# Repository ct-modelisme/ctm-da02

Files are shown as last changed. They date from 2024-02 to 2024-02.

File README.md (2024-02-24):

# CTM-DA02: Blacksmith environment command

The CTM-DA02 is a blacksmith electronic controller for modelrailway projects.
This electronic card is compatible with DCC & AC/DC train layouts.

## Licenses

The hardware is released under OpenHardware principes, and the software under OpenSource principes.

 - Hardware (PCB): [Creative Commons Attribution-ShareAlike 4.0 International License](http://creativecommons.org/licenses/by-sa/4.0/)
 - Software (Firmware): [GNU General Public License v3](https://www.gnu.org/licenses/)

## Current releases

 - Hardware (PCB): version 1.0
 - Software (Firmware): version 1.0

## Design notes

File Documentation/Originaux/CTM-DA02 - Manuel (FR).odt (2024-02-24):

CTM-DA02

Commande de forge

La carte CTM-DA02 est une carte de commande de forge. Elle permet de commander un forgeron animé (ex : Viessmann® 1514) et une LED imitation flamme (ex : Lapierre-Modélisme 10L5FL) tout en jouant un fichier son.

En cas de bogue, ou simplement si vous avez des suggestions, merci de me contacter à l’adresse :

cyrille.toulet@linux.com

# Fonctionnalités

- Commande par DCC ou par boutons poussoirs (déportés et/ou sur la carte) ;
- Sortie forgeron (12V) et LED imitation flamme (3V) ;
- Lecture d’un fichier audio lors de l’animation ;
- Fonctionnalité d’apprentissage dynamique des adresses DCC ;
- Connexion USB série 115 200 bauds (optionnelle).

# Montage

## Aperçu du montage minimal

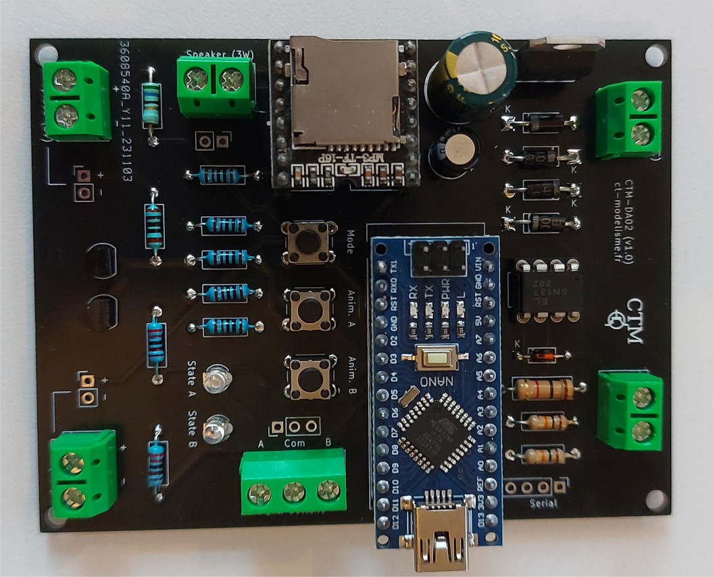
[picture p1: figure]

## Liste des composants

## Ordre de montage recommandé

Comme pour n’importe quel circuit électronique, commencez des composants les moins hauts pour terminer sur les plus hauts : diode 1N4148 (D5), puis résistances 1/4 W (toutes sauf R1), puis diodes 1N4007 (D1 à D4) et résistance 1W (R1). Ensuite, boutons poussoirs (SW1-3), supports de CI (s’il y en a), opto-coupleur (U2), LEDs (D6 et D7) , transistors (Q1 et Q2), connecteurs et borniers à vis, condensateurs 6.3mm (C2), condensateurs 10mm (C1) et enfin, le régulateur de tension 5V (U1). Terminez par enficher l’arduino (A1) et le lecteur audio (U3).

## Options

En fonction du câblage de votre réseau, vous pouvez opter pour presque chaque entrée/sortie entre tiliser un bornier, utiliser un connecteur tulippe ou à broche, ou encore souder des fils directement à la place du connecteur.

Ainsi, les connecteurs J3 et J4 sont reliés, ainsi que J6 avec J7, J8 avec J9, et J10 avec J11.

Pour rendre démontable le lecteur audio ou l’arduino, vous pouvez également ajouter les supports femelles préconisés dans la liste des compostants.

# Installation

## Firmware

Compilez et envoyez le firmware de la carte vers un arduino nano à partir de du logiciel Arduino SDK. Puis enfichez l’arduino sur le connecteur A1.

## Fixation

La carte électronique dispose de 4 trous de montage M3 pour être fixée avec des vis (avec ou sans entretoises) ou des supports édhésifs.

## Connexions

Connectez une alimentation de 12V DC sur le connecteur « Power » (peu importe la polarité). Connectez le bus JK sur le connecteur « DCC » (pas de polarité particulière). Connectez le haut-parleur (2 à 3W min sous 4 ou 8 Ohm) sur le connecteur « Spealer », la LED simulation de flame sur le connecteur « Fireplace » et le personnage animé sur le connecteur « Envil ». Vous pouvez aussis déporter un poutton poussoir pour lancer l’animation. Dans ce cas, connectez le sur le connecteur « Ext. buttons ».

# Utilisation

## Apprentissage d’adresse DCC

Pour entrer en mode apprentissage d’adresse, appuyez 3 secondes sur le bouton « Mode ». La LED « L » de l’arduino s’allume.

Envoyez une commande d’accessoire sur l’adresse voulue depuis votre centrale DCC. Cette adresse sera mémorisée par la carte comme adresse DCC de la carte.

Une fois l’adresse apprise, la carte repasse en mode normal et la LED « L » de l’arduino s’éteint.

Astuce : vous pouvez quitter à tout moment le mode apprentissage en appuyant 2 secondes sur le bouton « Mode ».

## Moniteur série & réinitialisation de la carte

Lorsque vous branchez un câble USB à l’arduino, et que vous lancez le moniteur série à 115 200 bauds, un appuis court sur le bouton « Mode » imprimera la configuration courante de la carte.

Différentes informations seront affichée suite à plusieurs appuis sur le bouton « Mode », jusqu’à revenir en fonctionnement normal.

Astuce : lors que vous utilisez le moniteur série, il est possible de réinitialiser la carte en tapant la commande « reset » dans la console. Cette commande aura pour effet de réinitialiser la carte à ses paramètres d’usine.

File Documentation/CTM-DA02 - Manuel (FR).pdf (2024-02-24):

# CTM-DA02

## Commande de forge

La carte CTM-DA02 est une carte de commande de forge. Elle permet de commander un forgeron animé (ex : Viessmann® 1514) et une LED imitation flamme (ex : Lapierre-Modélisme 10L5FL) tout en jouant un fichier son.
En cas de bogue, ou simplement si vous avez des suggestions, merci de me contacter à l’adresse : cyrille.toulet@linux.com

## Fonctionnalités

- Commande par DCC ou par boutons poussoirs (déportés et/ou sur la carte) ;
- Sortie forgeron (12V) et LED imitation flamme (3V) ;
- Lecture d’un fichier audio lors de l’animation ;
- Fonctionnalité d’apprentissage dynamique des adresses DCC ;
- Connexion USB série 115 200 bauds (optionnelle).

## Montage

## Aperçu du montage minimal

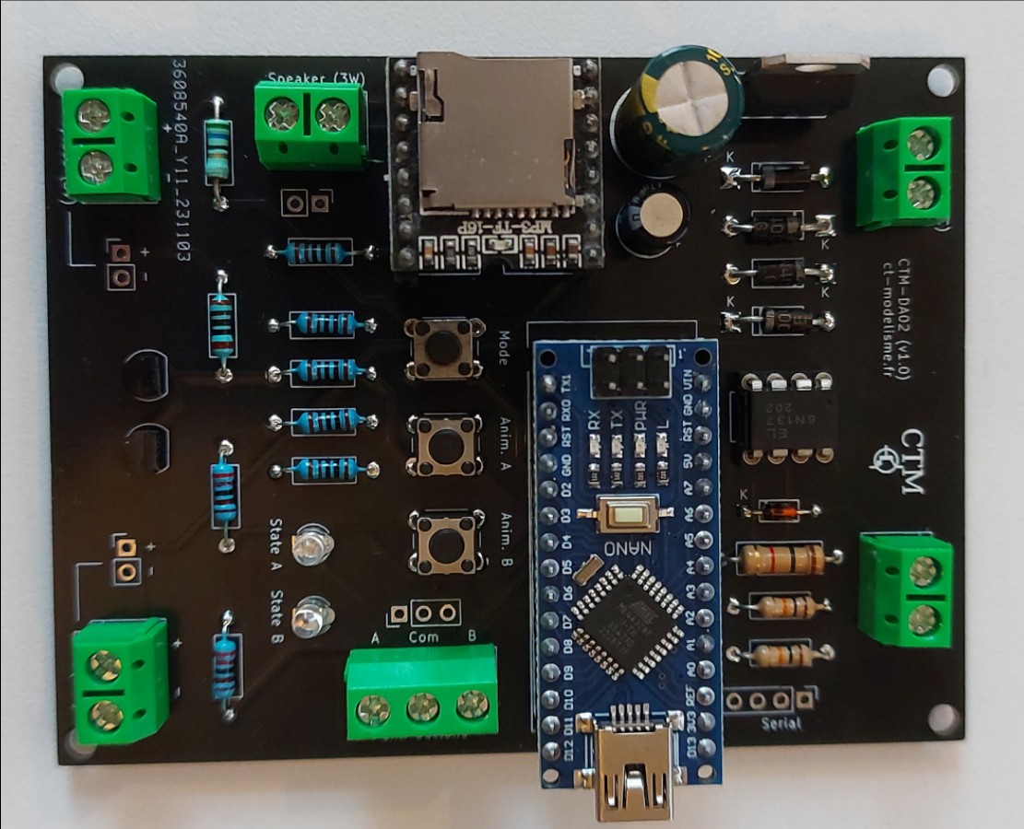
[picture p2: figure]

## Liste des composants

Options | Qté | Composant
A1 | 2 | Connecteur 15 pins femelle (pour rendre l’arduino démontable)
U3 | 2 | Connecteur 8 pins femelle (pour rendre le DFPlayer démontable)
J3 et/ou J4 | - | Soit rien, soit l'un, soit l'autre, soit les deux
J5 | - | Pour connexion série
J6 et/ou J7 | - | Soit rien, soit l'un, soit l'autre, soit les deux
J8 et/ou J9 | - | Soit rien, soit l'un, soit l'autre, soit les deux
J10 et/ou J11 | - | Soit rien, soit l'un, soit l'autre, soit les deux
Références | Composant | Quantité | Description
A1 | Arduino Nano | 1 | Support optionnel
C1 | 470µF | 1 | Diamètre 10mm, pas de 5mm
C2 | 10µF | 1 | Diamètre 6.3mm, pas de 2.5mm
D1, D2, D3, D4 | 1N4007 | 4
D5 | 1N4148 | 1
D6, D7 | LED | 2 | Diamètre 3mm
J1, J2, J7, J9, J10 | Bornier à vis 1x2 | 5 | Pas de 5.08mm
J3 | Bornier à vis 1x3 | 1 | Pas de 5.08mm
J4 | Connecteur tulipe 1x3 | 1 | Optionnel
J5 | Connecteur tulipe 1x4 | 1 | Optionnel
J6, J8, J11 | Connecteur tulipe 1x2 | 3 | Optionnel
Q1, Q2 | BC547 | 2 | Boîtier TO-92 en ligne
R1 | 1k (1W) | 1
R2, R3 | 10k | 2
R4, R5, R6, R7, R12 | 1k | 5
R8 | 56 | 1
R9 | 100 | 1
R10, R11 | 2.2k | 2
SW1, SW2, SW3 | Embeded push btn | 3 | Bouton 6mm
U1 | LM7805 (1A) | 1 | Boîtier TO-220
U2 | 6N137 | 1 | DIP-8
U3 | DFPlayerMini | 1 | Ou autre MP3-TF-16P
- | Carte micro-SD | 1 | Une petite suffira (ex : 512 Mo)
- | Haut parleur 2 à 3 W | 1 | 4 ou 8 Ohm
- | PCB CTM-DA02 | 1 | Carte électronique CTM-DA02

## Ordre de montage recommandé

Comme pour n’importe quel circuit électronique, commencez des composants les moins hauts pour terminer sur les plus hauts : diode 1N4148 (D5), puis résistances 1/4 W (toutes sauf R1), puis diodes 1N4007 (D1 à D4) et résistance 1W (R1). Ensuite, boutons poussoirs (SW1-3), supports de CI (s’il y en a), opto-coupleur (U2), LEDs (D6 et D7) , transistors (Q1 et Q2), connecteurs et borniers à vis, condensateurs 6.3mm (C2), condensateurs 10mm (C1) et enfin, le régulateur de tension 5V (U1). Terminez par enficher l’arduino (A1) et le lecteur audio (U3).

## Options

En fonction du câblage de votre réseau, vous pouvez opter pour presque chaque entrée/sortie entre tiliser un bornier, utiliser un connecteur tulippe ou à broche, ou encore souder des fils directement à la place du connecteur.
Ainsi, les connecteurs J3 et J4 sont reliés, ainsi que J6 avec J7, J8 avec J9, et J10 avec J11.
Pour rendre démontable le lecteur audio ou l’arduino, vous pouvez également ajouter les supports femelles préconisés dans la liste des compostants.

## Installation

## Firmware

Compilez et envoyez le firmware de la carte vers un arduino nano à partir de du logiciel Arduino SDK. Puis enfichez l’arduino sur le connecteur A1.

## Fixation

La carte électronique dispose de 4 trous de montage M3 pour être fixée avec des vis (avec ou sans entretoises) ou des supports édhésifs.

## Connexions

Connectez une alimentation de 12V DC sur le connecteur « Power » (peu importe la polarité). Connectez le bus JK sur le connecteur « DCC » (pas de polarité particulière). Connectez le haut-parleur (2 à 3W min sous 4 ou 8 Ohm) sur le connecteur « Spealer », la LED simulation de flame sur le connecteur « Fireplace » et le personnage animé sur le connecteur « Envil ». Vous pouvez aussis déporter un poutton poussoir pour lancer l’animation. Dans ce cas, connectez le sur le connecteur « Ext. buttons ».

## Utilisation

## Apprentissage d’adresse DCC

Pour entrer en mode apprentissage d’adresse, appuyez 3 secondes sur le bouton « Mode ». La LED « L » de l’arduino s’allume.
Envoyez une commande d’accessoire sur l’adresse voulue depuis votre centrale DCC. Cette adresse sera mémorisée par la carte comme adresse DCC de la carte.
Une fois l’adresse apprise, la carte repasse en mode normal et la LED « L » de l’arduino s’éteint. Astuce : vous pouvez quitter à tout moment le mode apprentissage en appuyant 2 secondes sur le bouton « Mode ».

## Moniteur série & réinitialisation de la carte

Lorsque vous branchez un câble USB à l’arduino, et que vous lancez le moniteur série à 115 200 bauds, un appuis court sur le bouton « Mode » imprimera la configuration courante de la carte. Différentes informations seront affichée suite à plusieurs appuis sur le bouton « Mode », jusqu’à revenir en fonctionnement normal.
Astuce : lors que vous utilisez le moniteur série, il est possible de réinitialiser la carte en tapant la commande « reset » dans la console. Cette commande aura pour effet de réinitialiser la carte à ses paramètres d’usine.

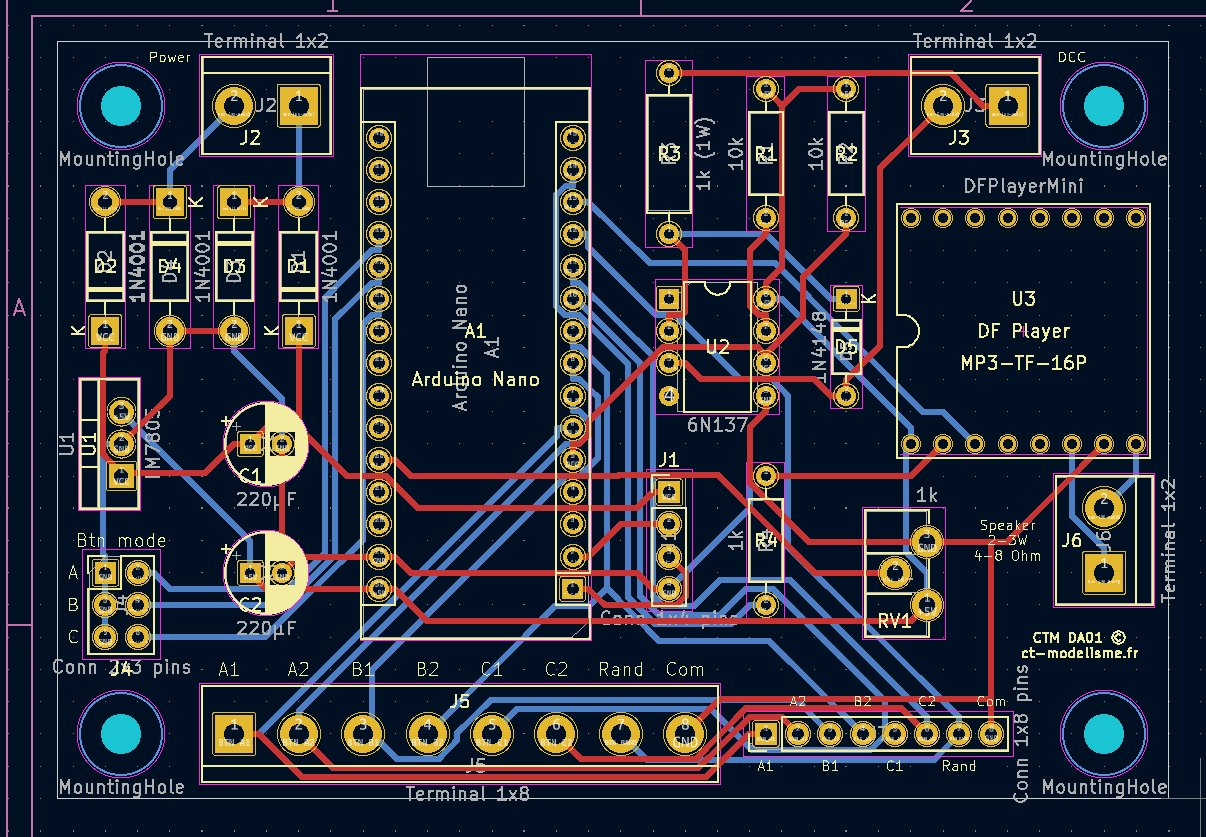
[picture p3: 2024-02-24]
Arduino/CTM-DA02/PCB DA01.PNG

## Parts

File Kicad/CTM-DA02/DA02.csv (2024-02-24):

Source: | C:\Users\Cyrille\Documents\KiCad\CTM - DA02\DA02\DA02.kicad_sch
Date: | 28/10/2023 11:12:37
Tool: | Eeschema (6.0.6)
Generator: | C:\Program Files\KiCad\6.0\bin\scripting\plugins/bom_csv_grouped_by_value.py
Component Count: | 45
Individual Components:
Item | Qty | Reference(s) | Value | LibPart | Footprint | Datasheet
 |  | A1 | Arduino Nano | MCU_Module:Arduino_Nano_v2.x | Module:Arduino_Nano | https://www.arduino.cc/en/uploads/Main/ArduinoNanoManual23.pdf
 |  | C1 | 470µF | Device:C_Polarized | Capacitor_THT:CP_Radial_D10.0mm_P5.00mm | ~
 |  | C2 | 10µF | Device:C_Polarized | Capacitor_THT:CP_Radial_D6.3mm_P2.50mm | ~
 |  | D1 | 1N4001 | Diode:1N4001 | Diode_THT:D_DO-41_SOD81_P10.16mm_Horizontal | http://www.vishay.com/docs/88503/1n4001.pdf
 |  | D2 | 1N4001 | Diode:1N4001 | Diode_THT:D_DO-41_SOD81_P10.16mm_Horizontal | http://www.vishay.com/docs/88503/1n4001.pdf
 |  | D3 | 1N4001 | Diode:1N4001 | Diode_THT:D_DO-41_SOD81_P10.16mm_Horizontal | http://www.vishay.com/docs/88503/1n4001.pdf
 |  | D4 | 1N4001 | Diode:1N4001 | Diode_THT:D_DO-41_SOD81_P10.16mm_Horizontal | http://www.vishay.com/docs/88503/1n4001.pdf
 |  | D5 | 1N4148 | Diode:1N4148 | Diode_THT:D_DO-35_SOD27_P7.62mm_Horizontal | https://assets.nexperia.com/documents/data-sheet/1N4148_1N4448.pdf
 |  | D6 | LED | Device:LED | LED_THT:LED_D3.0mm | ~
 |  | D7 | LED | Device:LED | LED_THT:LED_D3.0mm | ~
 |  | H1 | MountingHole | Mechanical:MountingHole | MountingHole:MountingHole_3.2mm_M3 | ~
 |  | H2 | MountingHole | Mechanical:MountingHole | MountingHole:MountingHole_3.2mm_M3 | ~
 |  | H3 | MountingHole | Mechanical:MountingHole | MountingHole:MountingHole_3.2mm_M3 | ~
 |  | H4 | MountingHole | Mechanical:MountingHole | MountingHole:MountingHole_3.2mm_M3 | ~
 |  | J1 | Terminal 01x02 | Connector:Screw_Terminal_01x02 | TerminalBlock:TerminalBlock_bornier-2_P5.08mm | ~
 |  | J2 | Terminal 01x02 | Connector:Screw_Terminal_01x02 | TerminalBlock:TerminalBlock_bornier-2_P5.08mm | ~
 |  | J3 | Terminal 01x03 | Connector:Screw_Terminal_01x03 | TerminalBlock:TerminalBlock_bornier-3_P5.08mm | ~
 |  | J4 | Connector 01x03 | Connector_Generic:Conn_01x03 | Connector_PinHeader_2.54mm:PinHeader_1x03_P2.54mm_Vertical | ~
 |  | J5 | Connector 01x04 | Connector_Generic:Conn_01x04 | Connector_PinHeader_2.54mm:PinHeader_1x04_P2.54mm_Vertical | ~
 |  | J6 | Connector 01x02 | Connector_Generic:Conn_01x02 | Connector_PinHeader_2.54mm:PinHeader_1x02_P2.54mm_Vertical | ~
 |  | J7 | Terminal 01x02 | Connector:Screw_Terminal_01x02 | TerminalBlock:TerminalBlock_bornier-2_P5.08mm | ~
 |  | J8 | Connector 01x02 | Connector_Generic:Conn_01x02 | Connector_PinHeader_2.54mm:PinHeader_1x02_P2.54mm_Vertical | ~
 |  | J9 | Terminal 01x02 | Connector:Screw_Terminal_01x02 | TerminalBlock:TerminalBlock_bornier-2_P5.08mm | ~
 |  | J10 | Terminal 01x02 | Connector:Screw_Terminal_01x02 | TerminalBlock:TerminalBlock_bornier-2_P5.08mm | ~
 |  | J11 | Connector 01x02 | Connector_Generic:Conn_01x02 | Connector_PinHeader_2.54mm:PinHeader_1x02_P2.54mm_Vertical | ~
 |  | Q1 | BC547 | Transistor_BJT:BC547 | Package_TO_SOT_THT:TO-92_Inline | https://www.onsemi.com/pub/Collateral/BC550-D.pdf
 |  | Q2 | BC547 | Transistor_BJT:BC547 | Package_TO_SOT_THT:TO-92_Inline | https://www.onsemi.com/pub/Collateral/BC550-D.pdf
 |  | R1 | 1k (1W) | Device:R | Resistor_THT:R_Axial_DIN0309_L9.0mm_D3.2mm_P12.70mm_Horizontal | ~
 |  | R2 | 10k | Device:R | Resistor_THT:R_Axial_DIN0207_L6.3mm_D2.5mm_P10.16mm_Horizontal | ~
 |  | R3 | 10k | Device:R | Resistor_THT:R_Axial_DIN0207_L6.3mm_D2.5mm_P10.16mm_Horizontal | ~
 |  | R4 | 1k | Device:R | Resistor_THT:R_Axial_DIN0207_L6.3mm_D2.5mm_P10.16mm_Horizontal | ~
 |  | R5 | 1k | Device:R | Resistor_THT:R_Axial_DIN0207_L6.3mm_D2.5mm_P10.16mm_Horizontal | ~
 |  | R6 | 1k | Device:R | Resistor_THT:R_Axial_DIN0207_L6.3mm_D2.5mm_P10.16mm_Horizontal | ~
 |  | R7 | 1k | Device:R | Resistor_THT:R_Axial_DIN0207_L6.3mm_D2.5mm_P10.16mm_Horizontal | ~
 |  | R8 | 56 | Device:R | Resistor_THT:R_Axial_DIN0207_L6.3mm_D2.5mm_P10.16mm_Horizontal | ~
 |  | R9 | 100 | Device:R | Resistor_THT:R_Axial_DIN0207_L6.3mm_D2.5mm_P10.16mm_Horizontal | ~
 |  | R10 | 2.2k | Device:R | Resistor_THT:R_Axial_DIN0207_L6.3mm_D2.5mm_P10.16mm_Horizontal | ~
 |  | R11 | 2.2k | Device:R | Resistor_THT:R_Axial_DIN0207_L6.3mm_D2.5mm_P10.16mm_Horizontal | ~
 |  | R12 | 1k | Device:R | Resistor_THT:R_Axial_DIN0207_L6.3mm_D2.5mm_P10.16mm_Horizontal | ~
 |  | SW1 | Embeded push btn | Switch:SW_Push | Button_Switch_THT:SW_PUSH_6mm | ~
 |  | SW2 | Embeded push btn | Switch:SW_Push | Button_Switch_THT:SW_PUSH_6mm | ~
 |  | SW3 | Embeded push btn | Switch:SW_Push | Button_Switch_THT:SW_PUSH_6mm | ~
 |  | U1 | LM7805 | Regulator_Linear:LM7805_TO220 | Package_TO_SOT_THT:TO-220-3_Vertical | https://www.onsemi.cn/PowerSolutions/document/MC7800-D.PDF
 |  | U2 | 6N137 | Isolator:6N137 | Package_DIP:DIP-8_W7.62mm | https://docs.broadcom.com/docs/AV02-0940EN
 |  | U3 | DFPlayerMini | CTM:DFPlayerMini | Module:DFRobot_DFPlayerMini_DFR0299 | https://wiki.dfrobot.com/DFPlayer_Mini_SKU_DFR0299
Collated Components:
Item | Qty | Reference(s) | Value | LibPart | Footprint | Datasheet
1 | 1 | A1 | Arduino Nano | MCU_Module:Arduino_Nano_v2.x | Module:Arduino_Nano | https://www.arduino.cc/en/uploads/Main/ArduinoNanoManual23.pdf
2 | 1 | C1 | 470µF | Device:C_Polarized | Capacitor_THT:CP_Radial_D10.0mm_P5.00mm | ~
3 | 1 | C2 | 10µF | Device:C_Polarized | Capacitor_THT:CP_Radial_D6.3mm_P2.50mm | ~
4 | 4 | D1, D2, D3, D4 | 1N4001 | Diode:1N4001 | Diode_THT:D_DO-41_SOD81_P10.16mm_Horizontal | http://www.vishay.com/docs/88503/1n4001.pdf
5 | 1 | D5 | 1N4148 | Diode:1N4148 | Diode_THT:D_DO-35_SOD27_P7.62mm_Horizontal | https://assets.nexperia.com/documents/data-sheet/1N4148_1N4448.pdf
6 | 2 | D6, D7 | LED | Device:LED | LED_THT:LED_D3.0mm | ~
7 | 4 | H1, H2, H3, H4 | MountingHole | Mechanical:MountingHole | MountingHole:MountingHole_3.2mm_M3 | ~
8 | 5 | J1, J2, J7, J9, J10 | Terminal 01x02 | Connector:Screw_Terminal_01x02 | TerminalBlock:TerminalBlock_bornier-2_P5.08mm | ~
9 | 1 | J3 | Terminal 01x03 | Connector:Screw_Terminal_01x03 | TerminalBlock:TerminalBlock_bornier-3_P5.08mm | ~
10 | 1 | J4 | Connector 01x03 | Connector_Generic:Conn_01x03 | Connector_PinHeader_2.54mm:PinHeader_1x03_P2.54mm_Vertical | ~
11 | 1 | J5 | Connector 01x04 | Connector_Generic:Conn_01x04 | Connector_PinHeader_2.54mm:PinHeader_1x04_P2.54mm_Vertical | ~
12 | 3 | J6, J8, J11 | Connector 01x02 | Connector_Generic:Conn_01x02 | Connector_PinHeader_2.54mm:PinHeader_1x02_P2.54mm_Vertical | ~
13 | 2 | Q1, Q2 | BC547 | Transistor_BJT:BC547 | Package_TO_SOT_THT:TO-92_Inline | https://www.onsemi.com/pub/Collateral/BC550-D.pdf
14 | 1 | R1 | 1k (1W) | Device:R | Resistor_THT:R_Axial_DIN0309_L9.0mm_D3.2mm_P12.70mm_Horizontal | ~
15 | 2 | R2, R3 | 10k | Device:R | Resistor_THT:R_Axial_DIN0207_L6.3mm_D2.5mm_P10.16mm_Horizontal | ~
16 | 5 | R4, R5, R6, R7, R12 | 1k | Device:R | Resistor_THT:R_Axial_DIN0207_L6.3mm_D2.5mm_P10.16mm_Horizontal | ~
17 | 1 | R8 | 56 | Device:R | Resistor_THT:R_Axial_DIN0207_L6.3mm_D2.5mm_P10.16mm_Horizontal | ~
18 | 1 | R9 | 100 | Device:R | Resistor_THT:R_Axial_DIN0207_L6.3mm_D2.5mm_P10.16mm_Horizontal | ~
19 | 2 | R10, R11 | 2.2k | Device:R | Resistor_THT:R_Axial_DIN0207_L6.3mm_D2.5mm_P10.16mm_Horizontal | ~
20 | 3 | SW1, SW2, SW3 | Embeded push btn | Switch:SW_Push | Button_Switch_THT:SW_PUSH_6mm | ~
21 | 1 | U1 | LM7805 | Regulator_Linear:LM7805_TO220 | Package_TO_SOT_THT:TO-220-3_Vertical | https://www.onsemi.cn/PowerSolutions/document/MC7800-D.PDF
22 | 1 | U2 | 6N137 | Isolator:6N137 | Package_DIP:DIP-8_W7.62mm | https://docs.broadcom.com/docs/AV02-0940EN
23 | 1 | U3 | DFPlayerMini | CTM:DFPlayerMini | Module:DFRobot_DFPlayerMini_DFR0299 | https://wiki.dfrobot.com/DFPlayer_Mini_SKU_DFR0299

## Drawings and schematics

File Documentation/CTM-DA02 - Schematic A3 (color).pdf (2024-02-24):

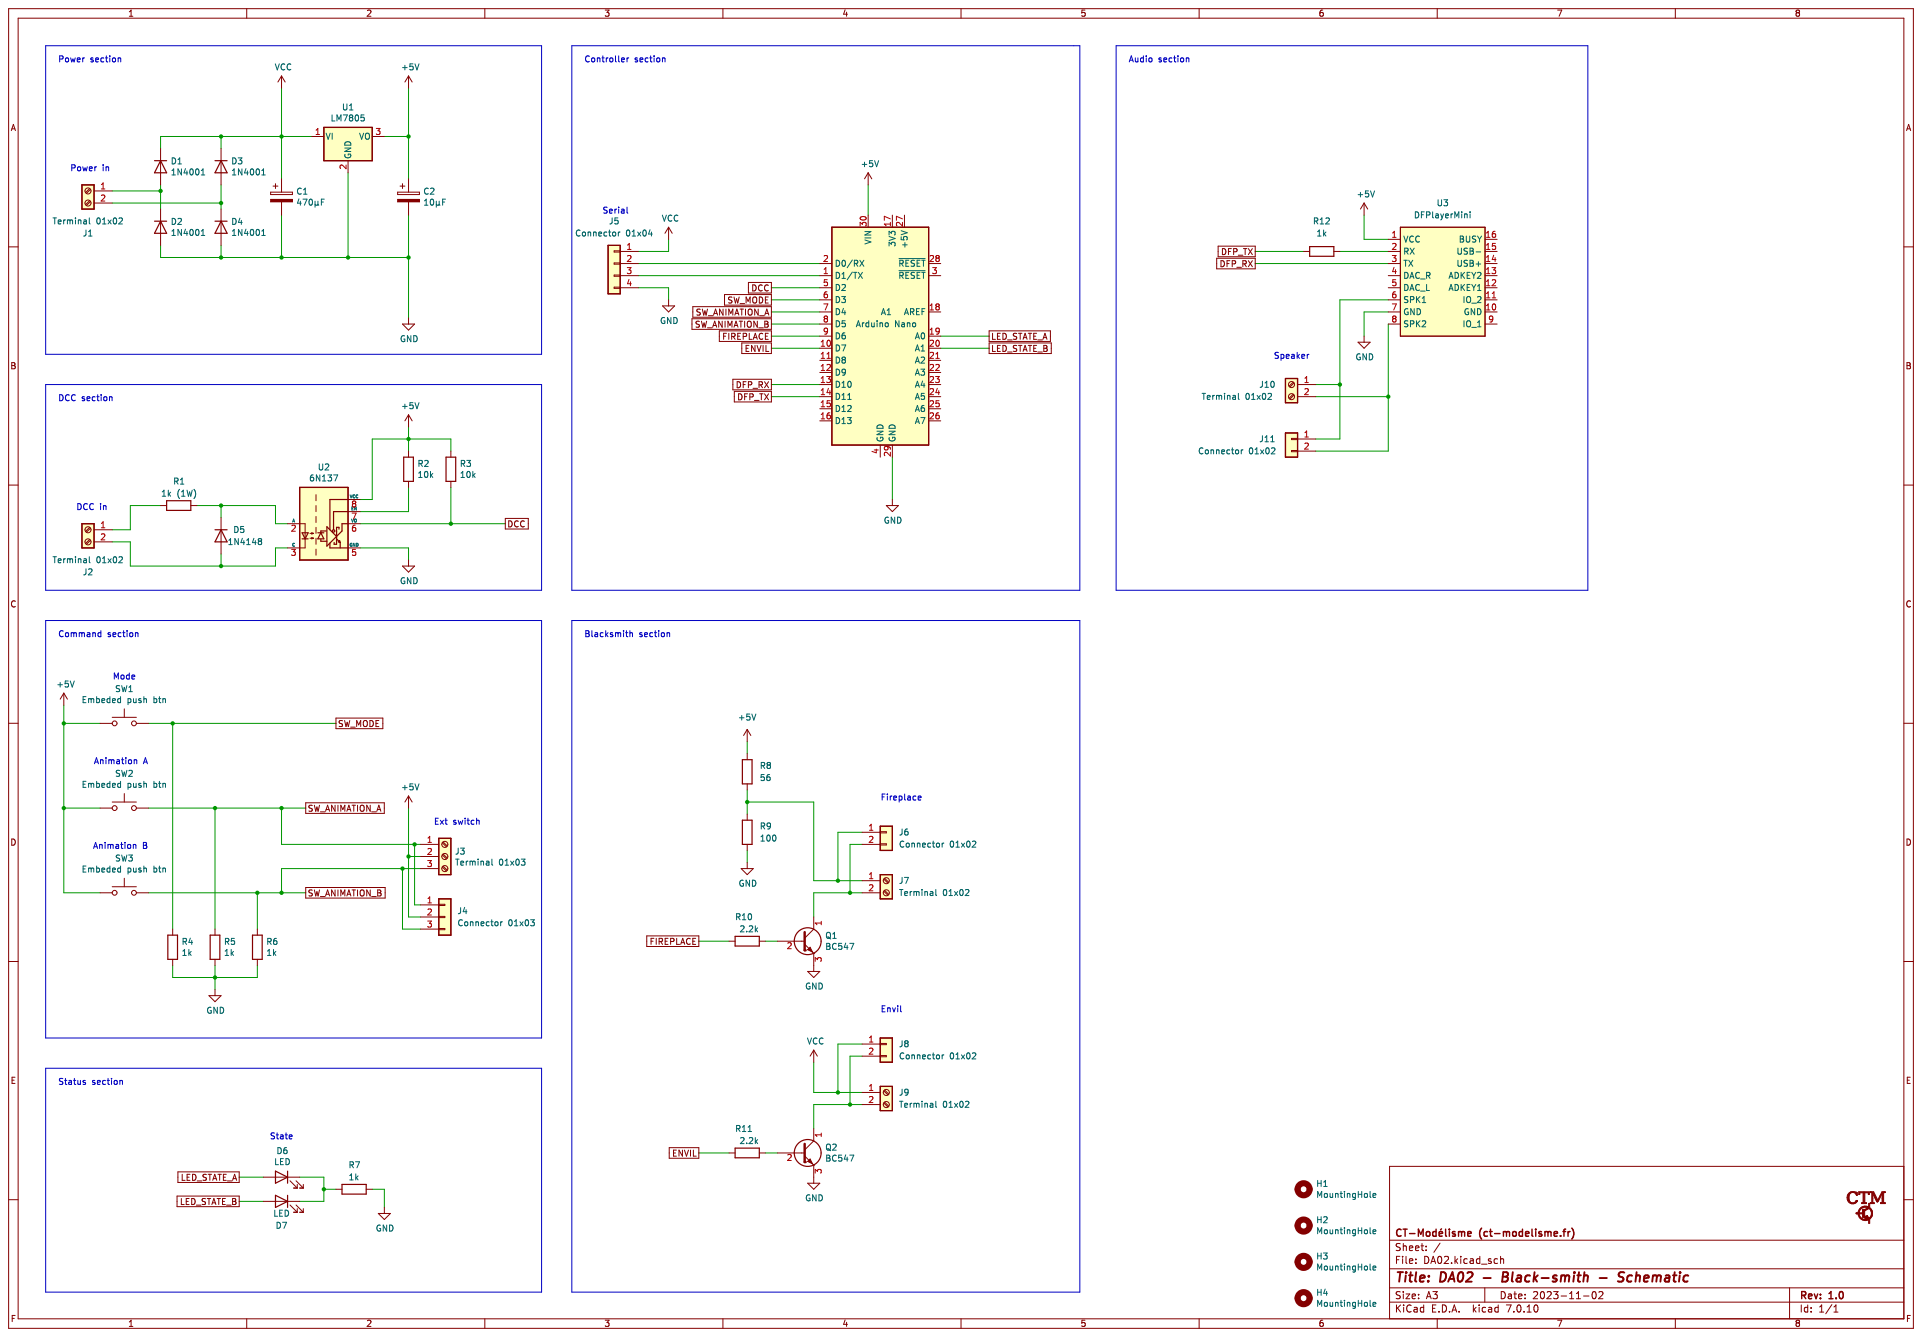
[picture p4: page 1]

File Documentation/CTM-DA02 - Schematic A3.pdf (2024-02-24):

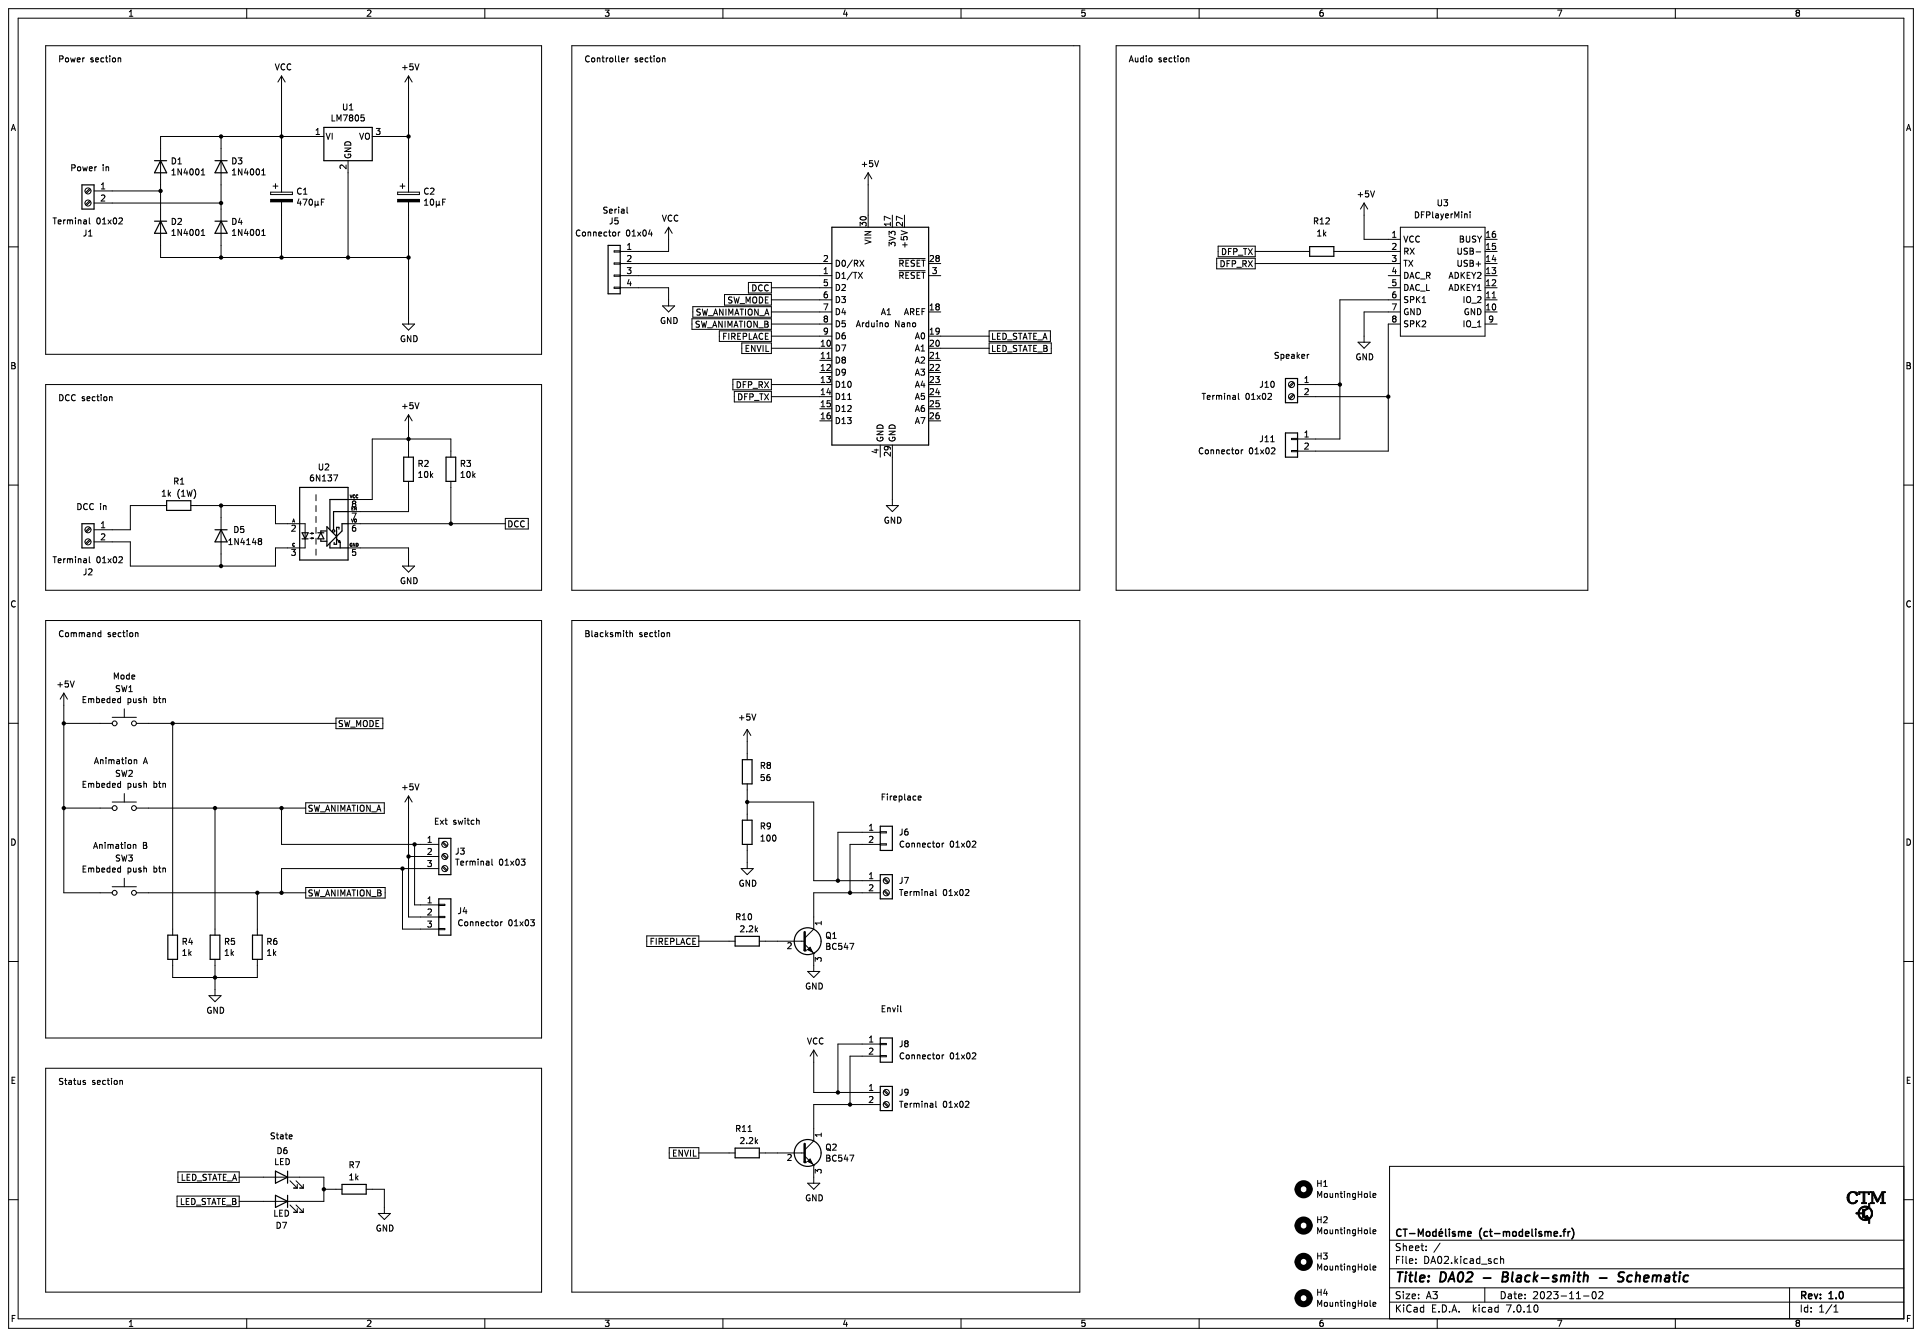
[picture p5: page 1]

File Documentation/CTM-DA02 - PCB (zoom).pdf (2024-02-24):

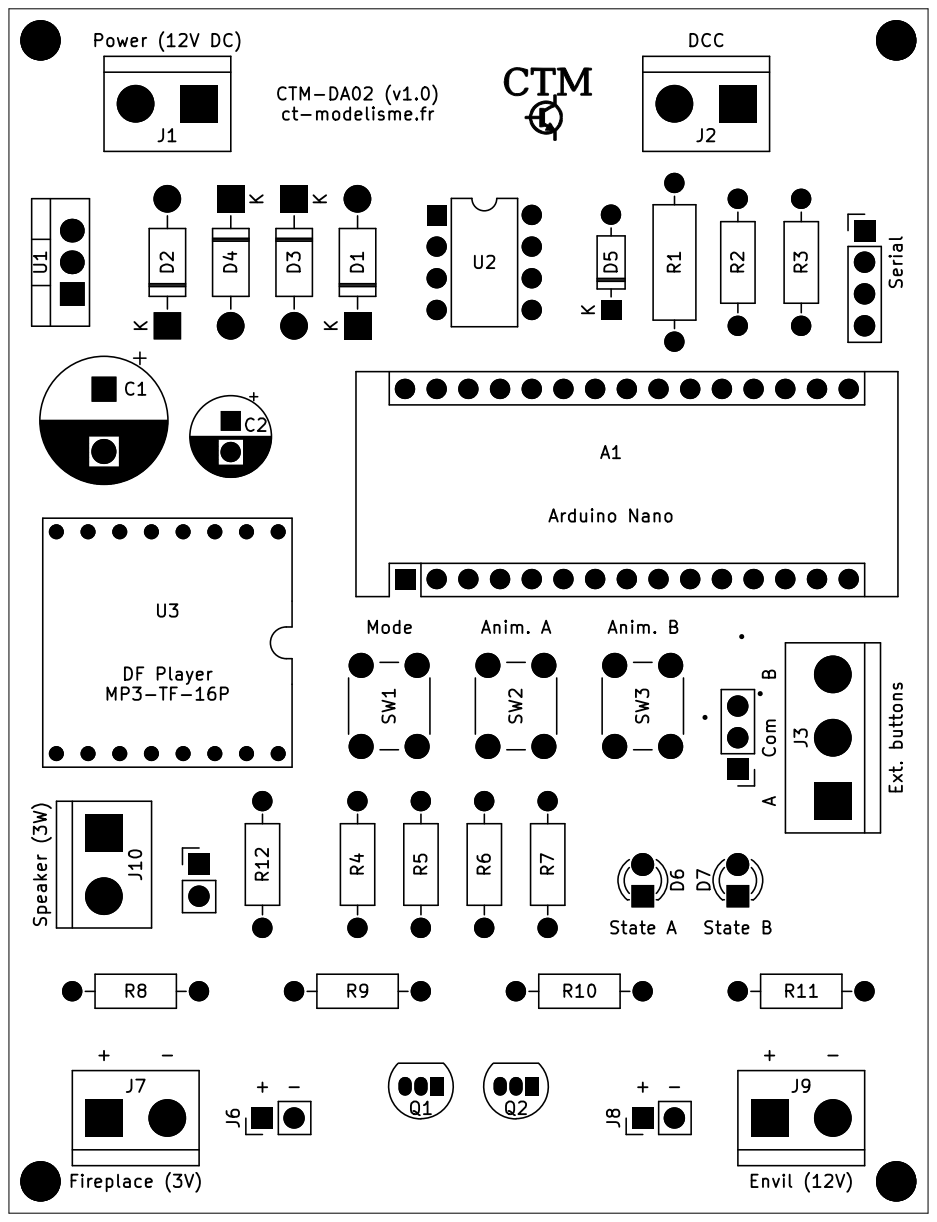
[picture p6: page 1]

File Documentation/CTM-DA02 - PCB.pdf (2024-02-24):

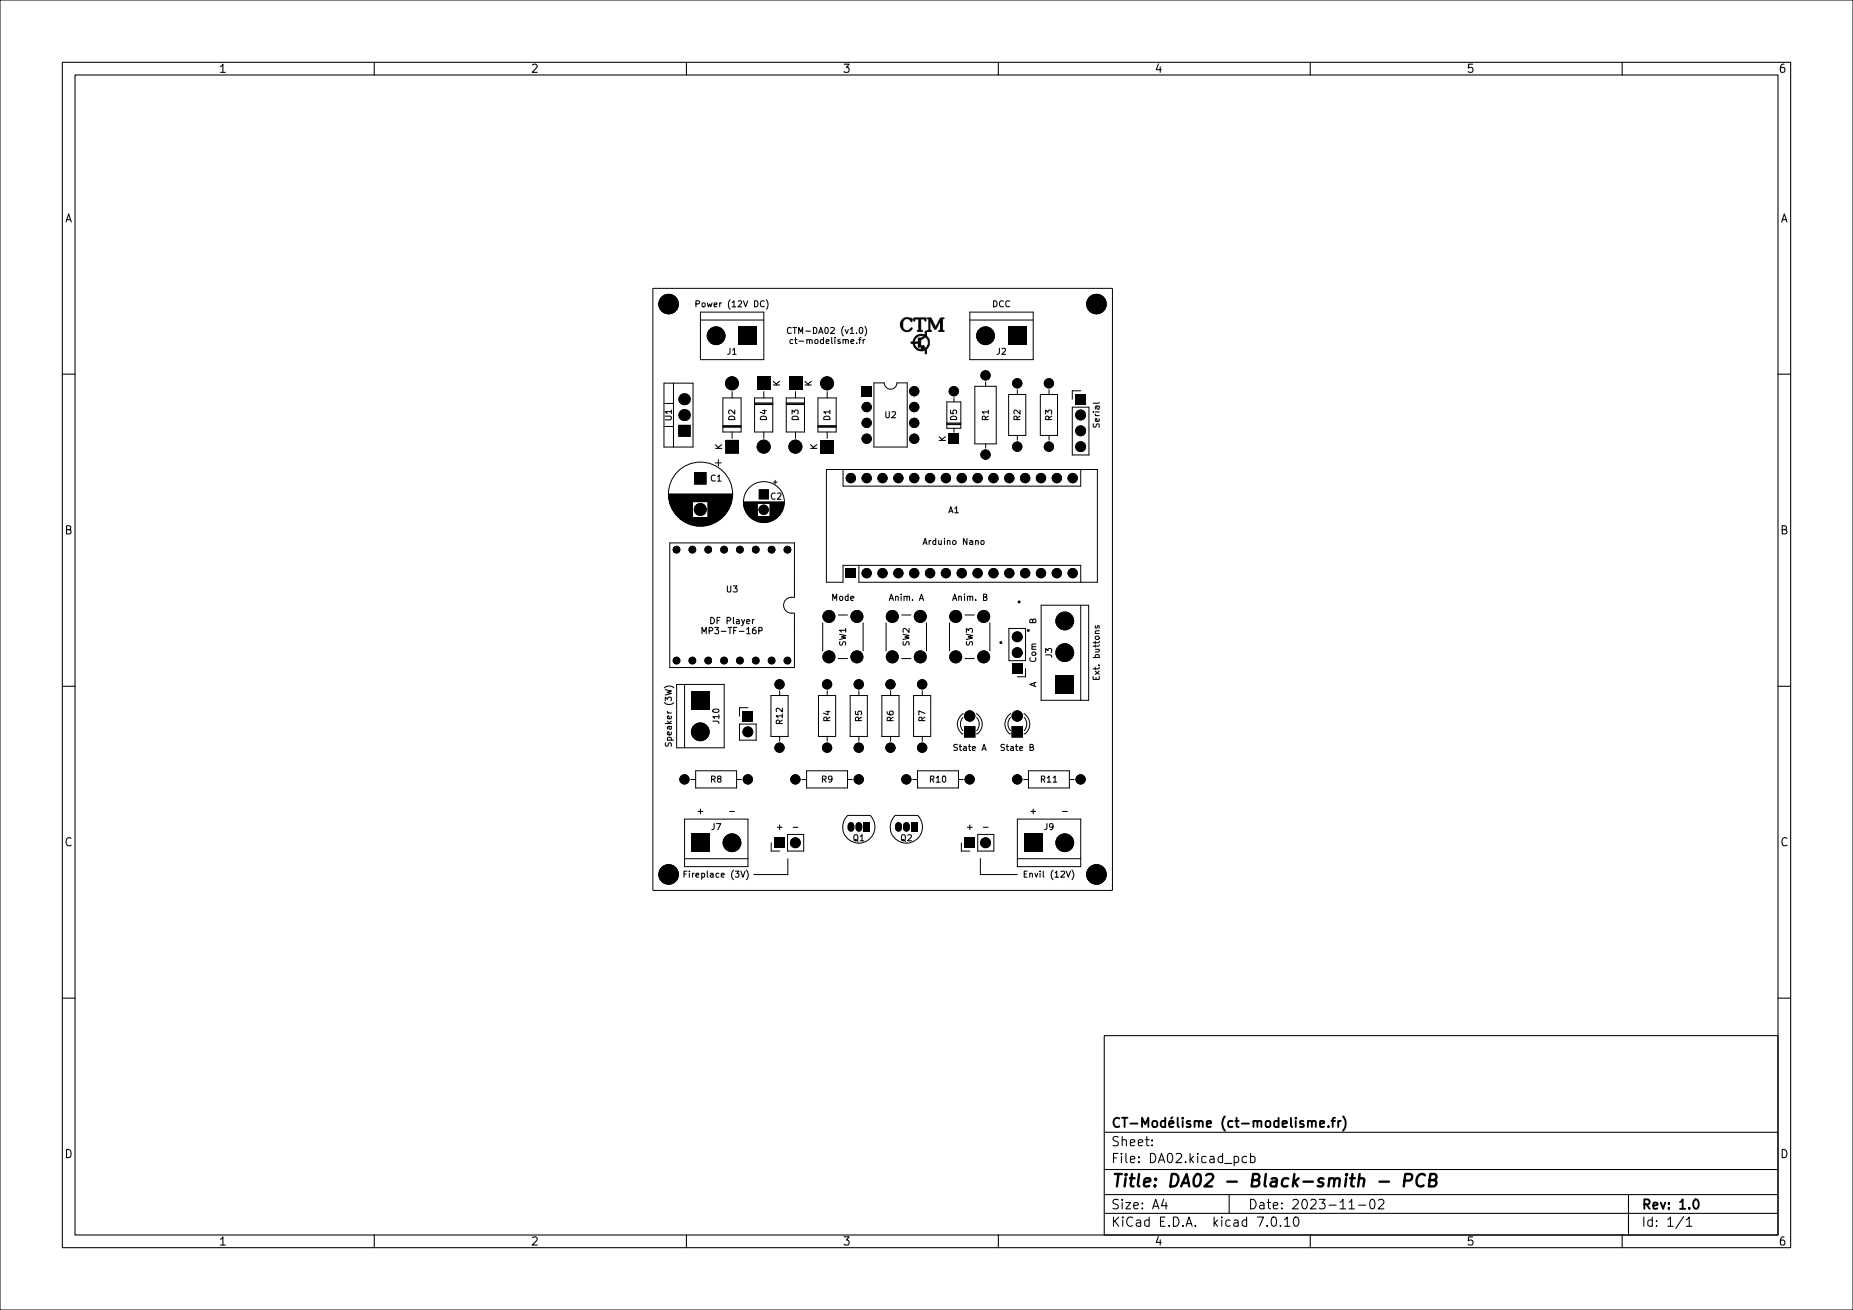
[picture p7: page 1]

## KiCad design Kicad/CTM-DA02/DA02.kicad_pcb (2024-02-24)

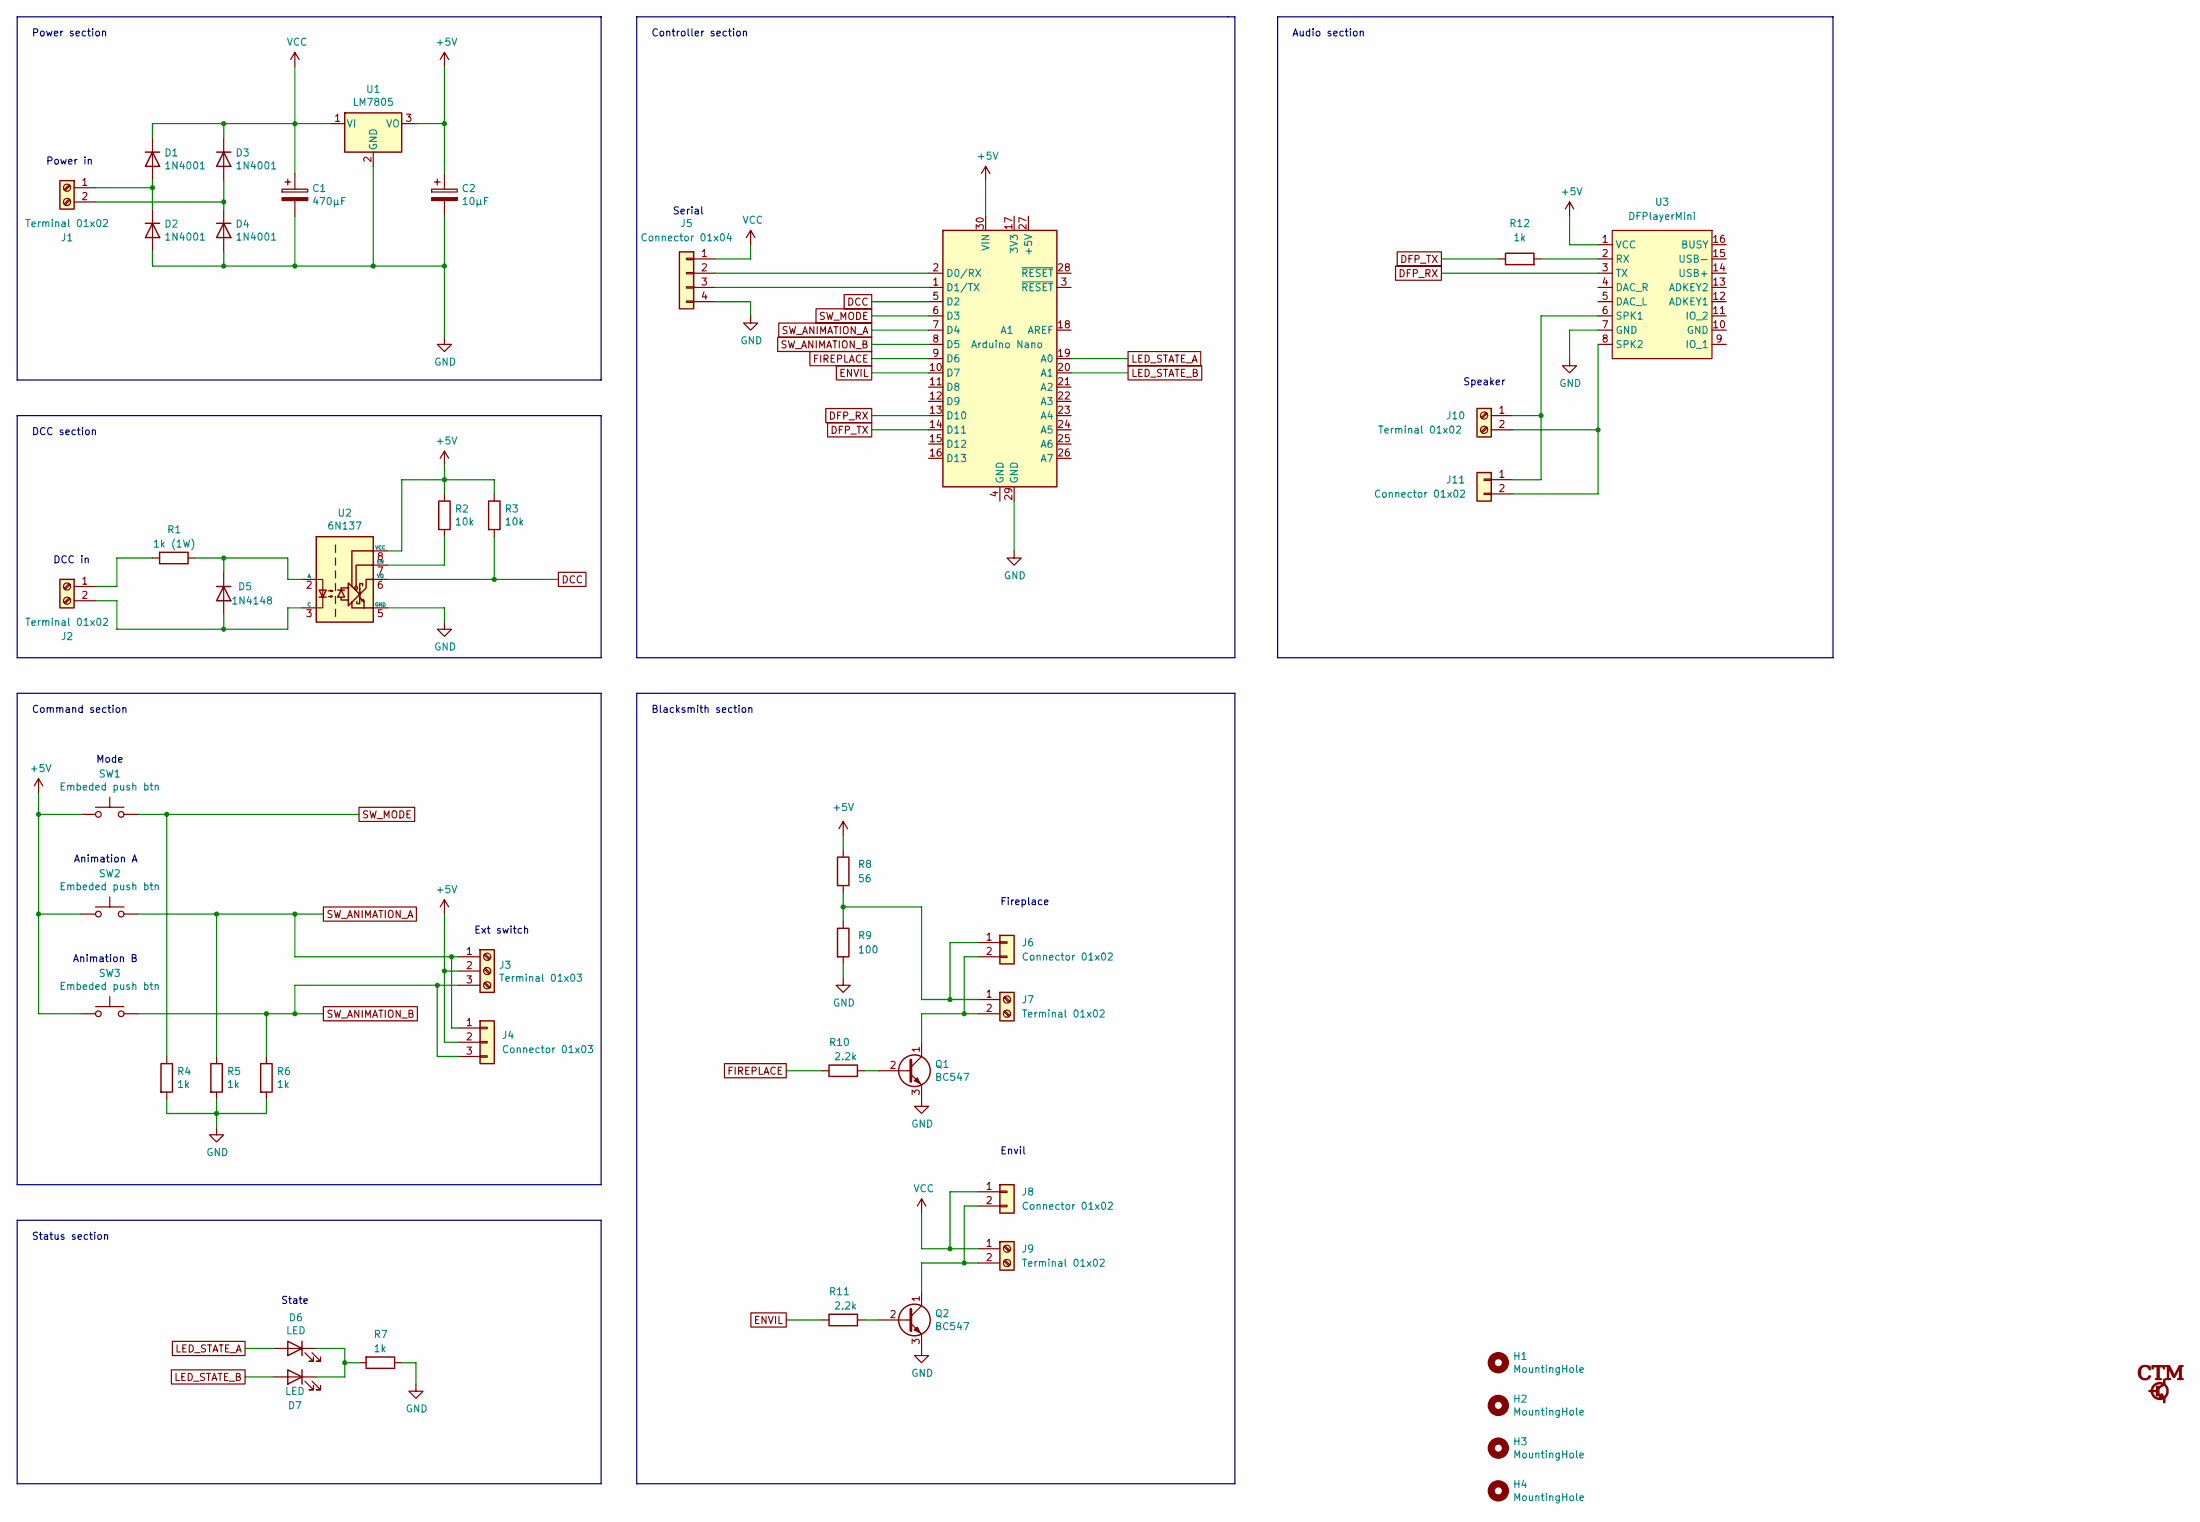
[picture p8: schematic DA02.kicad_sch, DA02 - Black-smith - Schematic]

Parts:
A1: Arduino Nano; Arduino_Nano
C1: 470µF; CP_Radial_D10.0mm_P5.00mm
C2: 10µF; CP_Radial_D6.3mm_P2.50mm
D1, D2, D3, D4: 1N4001; D_DO-41_SOD81_P10.16mm_Horizontal
D5: 1N4148; D_DO-35_SOD27_P7.62mm_Horizontal
D6, D7: LED; LED_D3.0mm
H1, H2, H3, H4: MountingHole; MountingHole_3.2mm_M3
J1, J2, J7, J9, J10: Terminal 01x02; TerminalBlock_bornier-2_P5.08mm
J3: Terminal 01x03; TerminalBlock_bornier-3_P5.08mm
J4: Connector 01x03; PinHeader_1x03_P2.54mm_Vertical
J5: Connector 01x04; PinHeader_1x04_P2.54mm_Vertical
J6, J8, J11: Connector 01x02; PinHeader_1x02_P2.54mm_Vertical
Q1, Q2: BC547; TO-92_Inline
R1: 1k (1W); R_Axial_DIN0309_L9.0mm_D3.2mm_P12.70mm_Horizontal
R2, R3: 10k; R_Axial_DIN0207_L6.3mm_D2.5mm_P10.16mm_Horizontal
R4, R5, R6, R7, R12: 1k; R_Axial_DIN0207_L6.3mm_D2.5mm_P10.16mm_Horizontal
R8: 56; R_Axial_DIN0207_L6.3mm_D2.5mm_P10.16mm_Horizontal
R9: 100; R_Axial_DIN0207_L6.3mm_D2.5mm_P10.16mm_Horizontal
R10, R11: 2.2k; R_Axial_DIN0207_L6.3mm_D2.5mm_P10.16mm_Horizontal
SW1, SW2, SW3: Embeded push btn; SW_PUSH_6mm
U1: LM7805; TO-220-3_Vertical
U2: 6N137; DIP-8_W7.62mm
U3: DFPlayerMini; DFRobot_DFPlayerMini_DFR0299

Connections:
+5V: A1.30 (VIN), C2.1, J3.2, J4.2, R2.1, R3.1, R8.1, SW1.1, SW2.1, SW3.1, U1.3 (VO), U2.8 (VCC), U3.1 (VCC)
DCC: A1.5 (D2), R3.2, U2.6 (VO)
DFP_RX: A1.13 (D10), U3.3 (TX)
DFP_TX: A1.14 (D11), R12.1
ENVIL: A1.10 (D7), R11.1
FIREPLACE: A1.9 (D6), R10.1
GND: A1.29 (GND), C1.2, C2.2, D2.2 (A), D4.2 (A), J5.4, Q1.3 (E), Q2.3 (E), R4.2, R5.2, R6.2, R7.1, R9.2, U1.2 (GND), U2.5 (GND), U3.7 (GND)
LED_STATE_A: A1.19 (A0), D6.2 (A)
LED_STATE_B: A1.20 (A1), D7.2 (A)
unnamed: A1.1 (D1/TX), J5.3
unnamed: A1.2 (D0/RX), J5.2
unnamed: D1.2 (A), D2.1 (K), J1.1
unnamed: D3.2 (A), D4.1 (K), J1.2
unnamed: D5.1 (K), R1.1, U2.2 (A)
unnamed: D5.2 (A), J2.2, U2.3 (C)
unnamed: D6.1 (K), D7.1 (K), R7.2
unnamed: J2.1, R1.2
unnamed: J6.1, J7.1, R8.2, R9.1
unnamed: J6.2, J7.2, Q1.1 (C)
unnamed: J8.2, J9.2, Q2.1 (C)
unnamed: J10.1, J11.1, U3.6 (SPK1)
unnamed: J10.2, J11.2, U3.8 (SPK2)
unnamed: Q1.2 (B), R10.2
unnamed: Q2.2 (B), R11.2
unnamed: R2.2, U2.7 (EN)
unnamed: R12.2, U3.2 (RX)
SW_ANIMATION_A: A1.7 (D4), J3.1, J4.1, R5.1, SW2.2
SW_ANIMATION_B: A1.8 (D5), J3.3, J4.3, R6.1, SW3.2
SW_MODE: A1.6 (D3), R4.1, SW1.2
VCC: C1.1, D1.1 (K), D3.1 (K), J5.1, J8.1, J9.1, U1.1 (VI)

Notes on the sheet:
Audio section
Command section
Status section
Power section
Animation B
Power in
Mode
Controller section
Fireplace
State
Envil
DCC in
Blacksmith section
Ext switch
Serial
Speaker
Animation A
DCC section

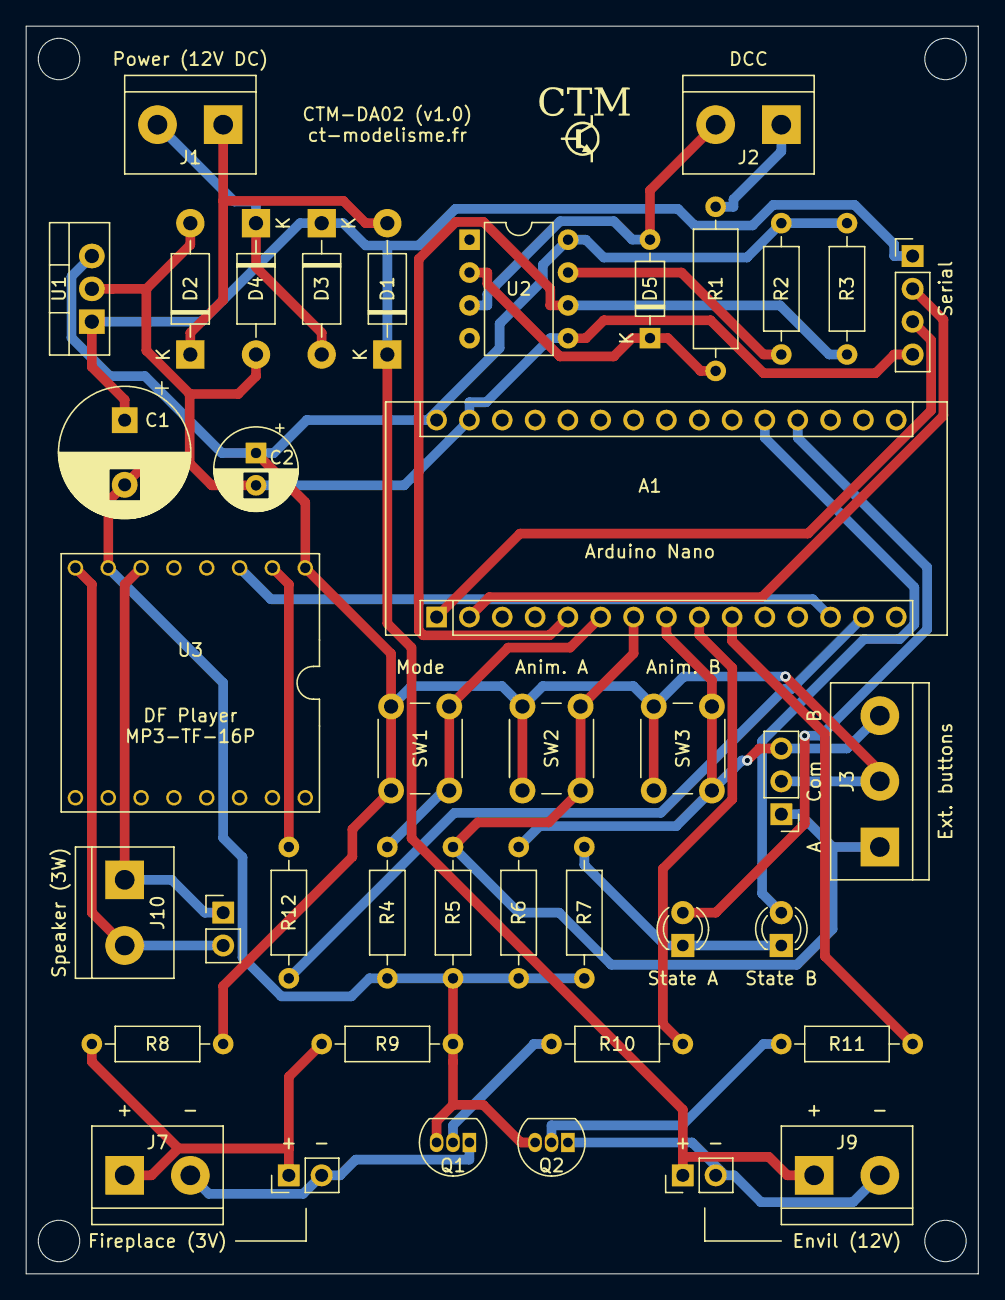
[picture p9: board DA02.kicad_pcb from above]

Board: 2 copper layers, 73.7 x 96.5 mm, 45 parts (0 on the bottom side), 30 nets.

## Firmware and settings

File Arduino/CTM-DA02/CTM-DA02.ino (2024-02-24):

/**
 * CT-Modelisme (ct-modelisme.fr) - Decodeur Audio 02 - Black-smith (CTM-DA02.ino)
 * 
 * Requires NmraDcc library from mrrwa (https://github.com/mrrwa/NmraDcc)
 * Requires Servo library from arduino project (https://www.arduino.cc/reference/en/libraries/servo/)
 * 
 * 
 * Copyright (C) 2021 Cyrille TOULET
 *
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
 * 
 * Cyrille TOULET <cyrille.toulet@linux.com>
 * Thu Nov 23 02:43:48 PM CET 2023
 */

#include "DCCInterface.h"
#include "AccessoryDecoder.h"
#include "CLI.h"


// Objects
CLI *cli;
DCCInterface *dcc;
AccessoryDecoder *decoder;


// Setup arduino
void setup()
{
  // Command line interface
  cli = CLI::getInstance();
  cli->setup();

  // DCC
  dcc = DCCInterface::getInstance();
  dcc->setup();

  // Accessory decoder
  decoder = AccessoryDecoder::getInstance();
  decoder->setup();
}


// Run main loop
void loop()
{
  cli->loop();
  decoder->loop();
  dcc->loop();
}

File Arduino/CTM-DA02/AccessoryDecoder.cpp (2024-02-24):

/**
 * CT-Modelisme (ct-modelisme.fr) - Decodeur Audio 02 - Black-smith (AccessoryDecoder.cpp)
 *
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
 * 
 * Cyrille TOULET <cyrille.toulet@linux.com>
 * Thu Nov 23 02:43:48 PM CET 2023
 */

#include "AccessoryDecoder.h"


// The factory CV values for this decoder
CV factoryCVs [] =
{
  {CV_ACCESSORY_DECODER_ADDRESS_LSB, 140},      // Less signifiant bits of long address 1
  {CV_ACCESSORY_DECODER_ADDRESS_MSB, 0},      // Most signifiant bits of long address 1
};


// Globals
SoftwareSerial playerSerial(
  PLAYER_RX_PIN, 
  PLAYER_TX_PIN
);


/**
 * Generic constructor for AccessoryDecoder
 */
AccessoryDecoder::AccessoryDecoder() 
{
  this->dcc = DCCInterface::getInstance();
  this->dcc->registerFactoryCVs(*factoryCVs, sizeof(factoryCVs) / sizeof(CV));
  
  this->mode = AccessoryDecoder::RUNNING;
  this->timerRunning = 0;
  
  // Read settings from decoder CVs
  this->dccAddress = this->dcc->readIntFromCVs(CV_ACCESSORY_DECODER_ADDRESS_LSB, CV_ACCESSORY_DECODER_ADDRESS_MSB);
}


/**
 * The deecoder setup function
 */
void 
AccessoryDecoder::setup()
{
  // Set pin modes
  pinMode(MODE_LED_OUT, OUTPUT);
  pinMode(STATE_A_LED_OUT, OUTPUT);
  pinMode(STATE_B_LED_OUT, OUTPUT);

  pinMode(FIREPLACE_OUT, OUTPUT);
  pinMode(ENVIL_OUT, OUTPUT);

  pinMode(MODE_BTN_IN, INPUT);
  pinMode(A_BTN_IN, INPUT);
  pinMode(B_BTN_IN, INPUT);

  Serial.println(" - Inputs/Outputs initialized");
  Serial.println("\nInitializing audio driver...");

  // Initialize DFPlayer
  playerSerial.begin(9600);
  // Initialize player with software serial, no ACK, and no reset (bug with reset)!!!
  if(!this->player.begin(playerSerial, false, false))
  {
    Serial.println(" - Error: unable to initialize driver. Is SD card inserted?\n");
    while(true);
  }

  Serial.println(" - MP3-TF-16P driver loaded");

  // Danger! There is a bug with reset function...
  //this->player.reset();
  this->player.setTimeOut(500);
  this->player.enableDAC();
  this->player.EQ(DFPLAYER_EQ_NORMAL);
  this->player.volume(15);

  Serial.println(" - MP3-TF-16P driver configured");

  Serial.println("Initializing completed!");
  Serial.print("CTM-DA02 - ");
  Serial.print("Firmware version: v");
  Serial.println(FIRMWARE);
  Serial.println("Please visit https://ct-modelisme.fr/\n");

  Serial.println("-- Running mode --");
}


/**
 * Parse audio player messages
 */
void 
AccessoryDecoder::parsePlayerMessages()
{
  if(this->player.available())
  {
    switch(this->player.readType())
    {
      case TimeOut:
        Serial.println("Time out!");
        break;
      case WrongStack:
        Serial.println("Stack wrong!");
        break;
      case DFPlayerCardInserted:
        Serial.println("Card inserted!");
        break;
      case DFPlayerCardRemoved:
        Serial.println("Card removed!");
        break;
      case DFPlayerCardOnline:
        Serial.println("Card online!");
        break;
      case DFPlayerError:
        Serial.print("DFPlayer error: ");
        switch (this->player.read()) {
          case Busy:
            Serial.println(F("card not found"));
            break;
          case FileMismatch:
            Serial.println(F("cannot find file"));
            break;
          default:
            break;
        }
        break;
      default:
        break;
    }
  }
}

/**
 * The deecoder loop
 */
void 
AccessoryDecoder::loop()
{
  // Running mode
  if(this->mode == RUNNING)
  {
    digitalWrite(MODE_LED_OUT, LOW);
    this->defineMode();

    if(digitalRead(A_BTN_IN))
    {
      Serial.println("First button pressed.");
      this->runAnimation();
      
      // Software anti-rebound
      do {
        delay(200);
      } while(digitalRead(A_BTN_IN));
    }
    
    if(digitalRead(B_BTN_IN))
    {
      Serial.println("Second button pressed (not implemented yet).");
      
      // Software anti-rebound
      do {
        delay(200);
      } while(digitalRead(B_BTN_IN));
    }
  }

  // Address prog mode
  else if(this->mode == ADDR_PROG)
    this->addressProgrammingMode();

  // Info mode
  else if(this->mode == INFO)
    this->informationMode();

  // Parse audio player messages
  this->parsePlayerMessages();
}



/**
 * Run main animation
 */
void
AccessoryDecoder::runAnimation()
{
  int id = 1;
  
  Serial.println("Running main animation.");

  digitalWrite(STATE_A_LED_OUT, HIGH);
  digitalWrite(FIREPLACE_OUT, HIGH);
  digitalWrite(ENVIL_OUT, HIGH);

  player.disableLoop();
  player.stop();
  // Bug si volume > à 20-25 (trop de courant consommé par l'ampli audio ???)
  player.volume(20);
  player.playFolder(1, id);
  
  this->animationState = 1;
  
  delay(55000);
  this->stopAnimation();
}



/**
 * Stop main animation
 */
void
AccessoryDecoder::stopAnimation()
{
  Serial.println("Stop main animation.\n");

  digitalWrite(STATE_A_LED_OUT, LOW);
  digitalWrite(STATE_B_LED_OUT, LOW);
  digitalWrite(FIREPLACE_OUT, LOW);
  digitalWrite(ENVIL_OUT, LOW);
  
  this->animationState = 0;
}



/**
 * Analyse buttons pressed or not and define the current mode
 */
void 
AccessoryDecoder::defineMode()
{
  if(this->mode == RUNNING)
  {
    int modeBtnValue = digitalRead(MODE_BTN_IN);
  
    // Start pressing mode button
    if(!this->timerRunning && modeBtnValue)
    {
      this->timerStartTime = millis();
      this->timerRunning = 1;
    }
    
    // Stop pressing mode button
    else if(this->timerRunning && !modeBtnValue)
    {
      this->timerEndTime = millis();
      this->timerRunning = 0;
      
      unsigned long duration = timerEndTime - timerStartTime;
  
      if(duration < 1000)
      {
        Serial.println("-- Information mode --");
        this->mode = INFO;
      }
      else
      {
        Serial.println("-- DCC Address programming mode --");
        this->mode = ADDR_PROG;
      }
    }
  }
}



/**
 * Information mode
 * Display settings on serial console.
 */
void 
AccessoryDecoder::informationMode()
{
  int modeBtnValue;
  
  Serial.print("DCC address: ");
  Serial.println(this->dccAddress);

  delay(200);
  do {
    modeBtnValue = digitalRead(MODE_BTN_IN);
  } while(modeBtnValue);
  
  // Software anti-rebound
  do {
    delay(200);
  } while(!digitalRead(MODE_BTN_IN));

  Serial.print("CTM-DA02 - ");
  Serial.print("Firmware version: v");
  Serial.println(FIRMWARE);

  delay(200);
  do {
    modeBtnValue = digitalRead(MODE_BTN_IN);
  } while(modeBtnValue);

  Serial.println("Back to running mode.\n");
  Serial.println("-- Running mode --");
  this->mode = RUNNING;
  
  // Software anti-rebound
  do {
    delay(200);
  } while(digitalRead(MODE_BTN_IN));
}
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

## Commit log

2024-02-24 Release first PCB version
    [DA02-B_Cu.gbr, DA02-B_Mask.gbr, DA02-Edge_Cuts.gbr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]
2024-02-24 Release first documentation version
    [CTM-DA02 - Bill Of Materials (FR).ods]

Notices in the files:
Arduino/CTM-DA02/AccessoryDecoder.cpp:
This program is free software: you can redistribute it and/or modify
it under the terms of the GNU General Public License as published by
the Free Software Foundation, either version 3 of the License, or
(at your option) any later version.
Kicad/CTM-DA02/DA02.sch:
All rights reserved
